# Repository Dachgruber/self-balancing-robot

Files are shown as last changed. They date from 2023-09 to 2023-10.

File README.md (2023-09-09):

# self-balancing-robot
Arduino code and building materials needed for the self-balancing-robot project for ElektronikFuerLA SoSe23 at CAU Kiel

## Hardware
The currently used hardware (MK1):
  -Arduino Nano (ATMega68p)
  -GY-521 Internal Measuring Unit
  -2x A4988 Stepper Motor Driver Boards
  -2x NEMA-17 0.48Nm Stepper Motors with D-Shaft
  -2200 mAh 40C 11.1V LiPo
  - 2 push buttons and 1 switch
  condensators, LEDs, wires...

Frame is build out of 10mm MDF-Plywood and 3mm craft wood sandwich plating
## Software

The code provided includes some testing programmes used at the R&D stage of development.

The finished piece of software will include:
  - a sensoring unit for measuring the current position
  - a calibration programm for calibrating said sensoring unit
  - a PID controller for controlling the two stepper motors
  - some form of remote control feature
and some more quality of life features

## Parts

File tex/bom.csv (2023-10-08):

Label | Part Type | mn | mpn | part number
C1 | Electrolytic Capacitor
LED1 | Red (633nm) LED
LED2 | Green (555nm) LED
M1 | Stepper Motor - Bipolar
M2 | Stepper Motor - Bipolar
Part1 | Arduino Nano (Rev3.0)
Part2 | InvenSense MPU6050
Pololu A2 | Pololu A4988
Pololu A3 | Pololu A4988
R1 | 220Ω Resistor
R2 | 330Ω Resistor
R3 | 10kΩ Resistor
R4 | 10kΩ Resistor
R5 | Rotary Potentiometer (Small)
S1 | Round Pushbutton
S2 | Taiway 100-SP-X-T1 SPDT Miniature Toggle Switch |  |  | 100-SP-X-T1-0-0-B1-M1
S3 | Round Pushbutton
U1 | LIPO-2000mAh
Amount | Part Type | mn | mpn | part number
2 | 10kΩ Resistor
1 | 220Ω Resistor
1 | 330Ω Resistor
1 | Arduino Nano (Rev3.0)
1 | Electrolytic Capacitor
1 | Green (555nm) LED
1 | InvenSense MPU6050
1 | LIPO-2000mAh
2 | Pololu A4988
1 | Red (633nm) LED
1 | Rotary Potentiometer (Small)
2 | Round Pushbutton
2 | Stepper Motor - Bipolar
1 | Taiway 100-SP-X-T1 SPDT Miniature Toggle Switch |  |  | 100-SP-X-T1-0-0-B1-M1

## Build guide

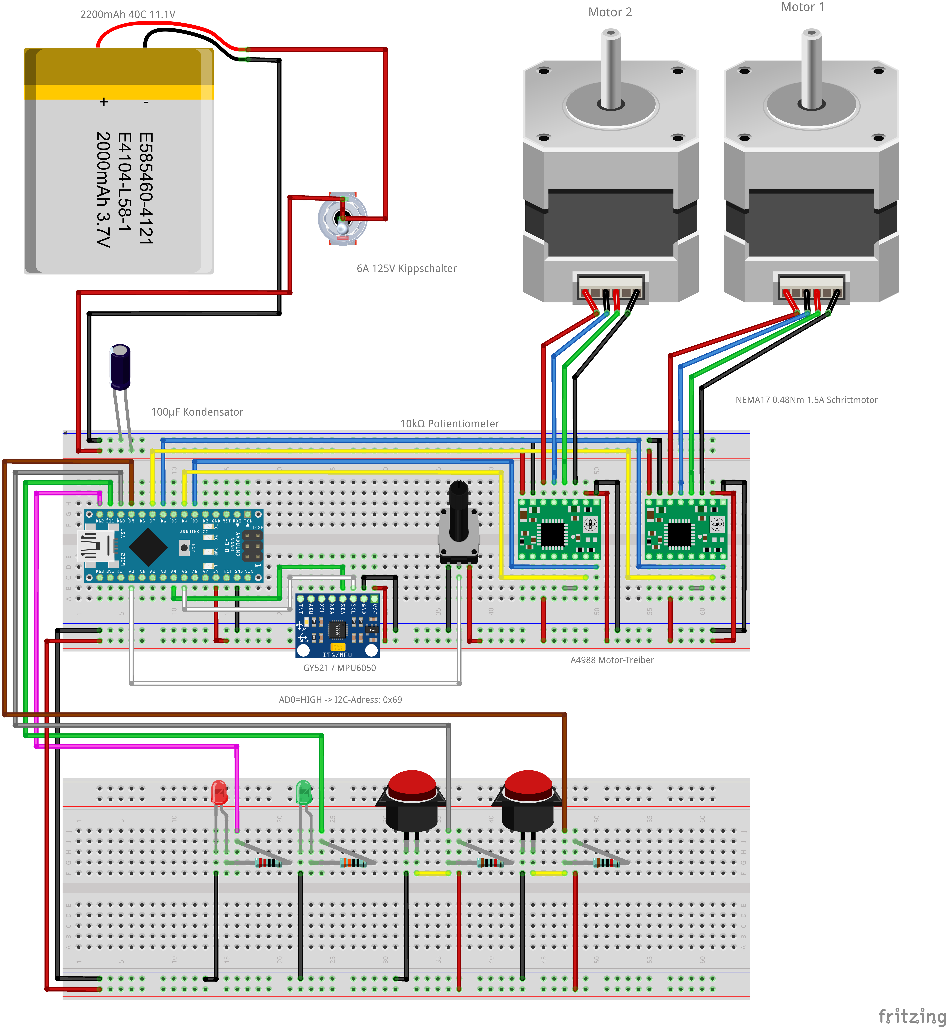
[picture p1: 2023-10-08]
tex/img/aufbau_breadboard.png

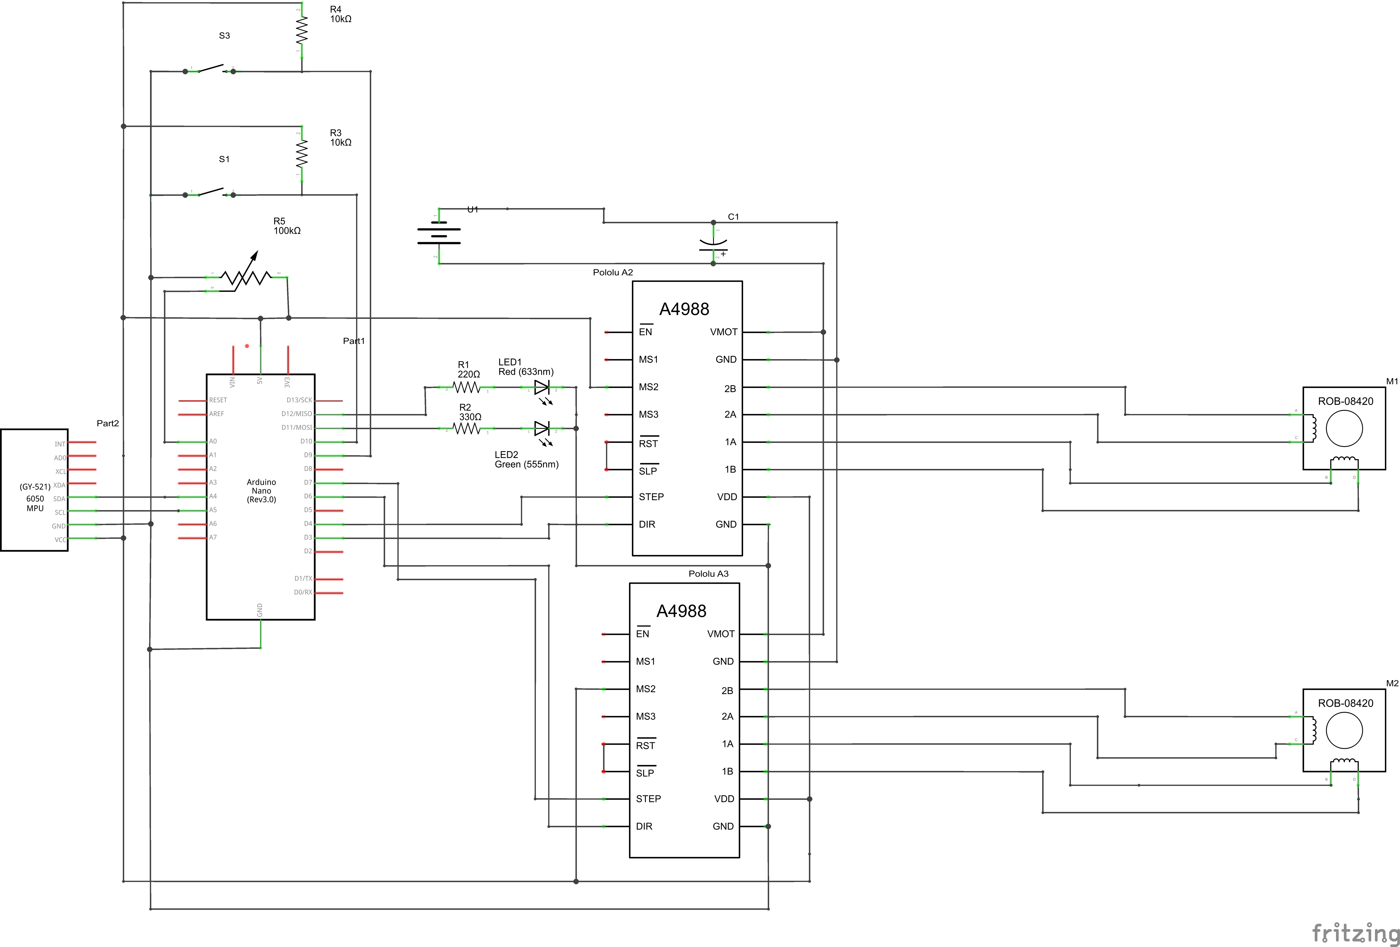
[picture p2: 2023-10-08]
tex/img/aufbau_scematic.png

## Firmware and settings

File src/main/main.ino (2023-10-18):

/*
* This is the main code used for the balancing robot. Flash this to the Arduino Nano Memory
* 
* This software will determine the current angle of the robot and will try to correct it to the desiredAngle constant usind the PID controller
*
* Used Wheels: d=70mm -> U = pi * d = 220mm
* Rotation = 200 Steps/rev * MicroStep -> 1000 Steps/rev
* 
* MaxSpeed = 1000 Steps/Second = 1 rev/s = 220mm/s
* 
* Höhe Schwerpunkt h = 240mm
* Schräglage theta = 20 degrees
*
* Zu korrigierende Länge x = h * sin (theta) = 82.08mm
*
* --> Bei einer Schräglage von 20 Grad ist Aropa theoretsch im Stande, die notwendige Länge bei MaxSpeed = 1000 in 0.4s zu überwinden
*
*/
//=============================================HEAD=======================================================
//used libraries
#include "math.h" 
#include <AccelStepper.h>
#include "KalmanMPU6050.h"
#include <PID_v1.h>

//math constants
#define earthConst 9.81

//DEBUG MODE enables serial output
const bool DEBUG = true;

//-----------------------------------------------Pins----------------------------------------------------

//two motor driver boards on two set of pins
#define dirPin1 3
#define stepPin1 4
#define dirPin2 6
#define stepPin2 7

#define potiPin A0

//no pins for the MPU as it gets detected on the I2C Bus
//#########################################CONFIG/TUNING ZONE###############################################

// params for the steppies
const int microStepConfiguration = 4; //1 for fullstep, 2 for halfstep, 4 for quarterstep...
const float maxSpeedLimit = 360 * microStepConfiguration * 2;
const float maxAccelLimit = 8000;

// three dabloons for the three parameters of the P I D
float KP = 16;   //(P)roportional Tuning Parameter
float KI = 0;   //(I)ntegral Tuning Parameter 
float KD = 0.0; //(D)erivative Tuning Parameter

//this is the angle in degrees the robot should be standing at, measured perpendicular to ground.
//the bias is used to account for a slanted positioning of the MPU (determine this using the mpu test) 
float angleBias = -2.5;
float targetAngle = 0 + angleBias;


//##########################################################################################################


//---------------------------------------------stepper setup----------------------------------------------

//stepper Objects used in the code
AccelStepper rightStep(AccelStepper::DRIVER,stepPin2,dirPin2);
AccelStepper leftStep(AccelStepper::DRIVER,stepPin1,dirPin1);  

//working var that specifies the current motorPower
volatile int motorPower;

//---------------------------------------------sensor setup----------------------------------------------
//working vars for the accelerometer and gyro
volatile float theta;


//-----------------------------------------------PID setup----------------------------------------------
//find KI,KP and KP in the Config Zone (tm)

//error working vars for the PID algorithm
volatile float error, prevError = 0, errorSum = 0;

//some time working vars //TODO: currently unused?
unsigned long currTime, prevTime = 0, loopTime;
float sampleTime = 0.005;

//find the desired angle in the Config Zone (tm)

//values used for the complimentary filter
float time = 0.9;
float alpha = time / (time + sampleTime);
float currentAngle, previousAngle;


//PID vars
//Define Variables we'll be connecting to
double setpoint, input, output;

//Specify the links and initial tuning parameters
PID myPID(&input, &output, &setpoint,2,5,1, DIRECT);
//============================================= TWIDDLE =======================================================

#include "Twiddle.h"
//const  bool AutoTuning = true;  // sets Twiddle on
const bool AutoTuning = false;

Twiddle Tuning(3,     KP,    KI,    KD, 0, 0, 0, 0, 0, 
                    0.005, 0.001, 0.001, 0,0,0,0,0);
//============================================= BODY =======================================================

void setup() {

  //because we do not want to explode the steppies
  rightStep.setMaxSpeed((float)maxSpeedLimit);
  leftStep.setMaxSpeed((float)maxSpeedLimit);

  //init the current Position
  leftStep.setCurrentPosition(0);
  rightStep.setCurrentPosition(0);

  //and determine the acceleration constant
  leftStep.setAcceleration(maxAccelLimit);
  rightStep.setAcceleration(maxAccelLimit);

  Serial.begin(9600);
  //Wire object is included the IMU lib atm
  //Wire.begin();
  //delay(100); //delay to rule out some issues with Wire being slow

  //mpu setup
  IMU::init();
  IMU::read();

  //enable the ISR timer routine
  initISR();

  //PID lib inits
  input = 0;
  setpoint = targetAngle;  
  myPID.SetOutputLimits(-360, 360);
  myPID.SetControllerDirection(1);

  Serial.println("SETUP COMPLETED");
  delay(1000);

}


/*
* util function that works like map, but for floats instead of integers
*/
float floatMap(float x, float in_min, float in_max, float out_min, float out_max) {
  return (x - in_min) * (out_max - out_min) / (in_max - in_min) + out_min;
}


/*
* Reads the onboard potentiometer and maps the analog value
* to a float between minV and maxV
*
*/
float readPoti(int minV, int maxV) {
  int analogValue = analogRead(potiPin);
  float finValue = floatMap(analogValue, 0, 1023, minV, maxV);

  return finValue;
}


void loop() {

  //read the tuning value of the poti
  //KP = readPoti(0,50);
  
  KD = readPoti(0,5);

  if  (AutoTuning)  PIDAutoTuning();  

  if (DEBUG) {
    Serial.print("KP:"); Serial.print(KP); Serial.print(" "); 
    Serial.print("KI:"); Serial.print(KI); Serial.print(" ");
    Serial.print("KD:"); Serial.print(KD); Serial.print(" ");
  }

  //Reads the data from the MPU...
  IMU::read();

  //...and processes it with the Kalman Filter
  theta = IMU::getRoll();

  //compute the needed motorpower using the PID
  //this sets the global motorPower to a new value
  //computePID();

  myPID.SetMode(AUTOMATIC);
  myPID.SetTunings(KP,KI,KD);
  input = theta;
  myPID.Compute();
  motorPower = output;

    if (DEBUG) {
    Serial.print("Current_Angle:");
    Serial.print(theta);
    Serial.print(",");
    Serial.print("Motor_Power:");
    Serial.println(motorPower);
  }


  //and set the Motors using the motorPower variable
  setMotors(motorPower, motorPower);

}

/* some register magic taken and from instructables and modified to my needs
*  LINK: https://www.instructables.com/Arduino-Self-Balancing-Robot-1/
* 
*  This enables the internal Timer1 to interrupt the loop routine every 5ms
*  The time depends on the setting of the prescaler TCCR1B and the Counting 
*  register OCR1A
*  
*  Example Calculations (for 500ms): 
*  System clock 16 Mhz and Prescalar 256;
*  Timer 1 speed = 16Mhz/256 = 62.5 Khz    
*  Pulse time = 1/62.5 Khz =  16us  
*  Count up to = 500ms / 16us = 31250 (so this is the value the OCR register should have)  
*/
void initISR(){
  cli(); // disable global interrupts
  TCCR1A = 0; //set entire TCCR1A register to 0, resetting the timer value
  TCCR1B = 0; //same for TCCR1B
  //set compare match register to set sample time 5ms
  OCR1A = 100;
  //prescale: will divide the clock signal with 8, slightly slowing down our timer
  //TCCR1B |= (1 << CS11);
  TCCR1B |= B00000010;
  // enable timer compare interrupt
  TIMSK1 |= (1 << OCIE1A);
  sei(); //enable global interrupts

} 

/*
* The Interrupt Service Routine (ISR) looks like a function
* that gets called in the specified timing intervall
*
* Our ISR will be called every 5ms to execute our run()
*/
ISR(TIMER1_COMPA_vect) {
  TCNT1  = 0; //reset the timer 
  // calling run() instead of runSpeed() tells the stepper to
  // accelerate to maxSpeed instead of using constant Speed
  leftStep.run();
  rightStep.run();

}
/*
* computes the new motorPower value using a PID-algorithm 
* We currently do not depend on the ISR for this call but instead call the PID function 
* from the main loop func ourselfs. This means that is isnt quite clear how much time
* lays inbetween calls, which will cause troubles later (foreshadowing)
*
* -> motorPower is a global variable because it needs to be when using the ISR
*
* This algorithm will do the following steps:
*
*     1. take the measured (and filtered!) angle from the mpu
*     2. compute the PID error that specifies, how "bad" the current situation is
*     3. compute the Proportional, Integral and Derivative terms of the PID with the magic KP,KI and KD numbers and errors
*     4. add the terms (and constrain the result!) the to calculate the needed motorPower (no return needed as motorPower is global)
*/
void computePID() {  

  /*1. take the angle */
  currentAngle = theta;

  if (DEBUG) {
    Serial.print("Current_Angle:");
    Serial.print(currentAngle);
    Serial.print(",");
  }

  /*2. error calculation*/
  //calculation of error values for the PID
  error = currentAngle - targetAngle;
  errorSum = errorSum + error;
  errorSum = constrain(errorSum, -300, 300); //damit uns die Geschichte nicht um die Ohren fliegt

  /*3. error calculation*/
  //calculate output from P, I and D values
  float pValue,iValue,dValue;
  pValue = KP * (error);
  iValue = KI * (errorSum)*sampleTime;
  dValue = KD * (currentAngle-previousAngle)/sampleTime;

  /*4. final steps*/
  float output = pValue + iValue - dValue;
  //a circle has 360 degrees, so constrain to one circle in each direction
  motorPower = constrain(output, -360, 360); 
  previousAngle = currentAngle; //save for next time

}

/*
* Function for controlling the left and right motor using a distance in degrees (°)
* positive values mean forward, negative mean backward rotation
*
*/
void setMotors(float leftDistance, float rightDistance){

  leftStep.move(leftDistance);
  rightStep.move(-rightDistance);

}

void  PIDAutoTuning()  //Twiddle Auto Tuning
// --------------------------------------------------------------
{
  static int skipT = 0;
  skipT++;
  if (skipT > 10) {
    skipT = 11;

    // average = Tuning.next( Robot.PositionAB, PidParams.Kp , PidParams.Ki , PidParams.Kd  ,  PidParams.Ka , PidParamsPos.Kp , PidParamsPos.Ki , PidParamsPos.Kd , PidParamsPos.Ka  );

    average = Tuning.next( (currentAngle), KP  , KI , KD , 0, 0 , 0  , 0 ,  0  );

  }
}



/*
* @deprecated
* This adds the gyro and accel angle using a comp filter
*
*/
//float addAngle(float gyro, float accel) {

  //calc the current angle depending on the measured data

  //accAngle = atan2(accY, accZ)*RAD_TO_DEG;
  //gyroRate = map(gyroX, -32768, 32767, -250, 250); //mapping gyroX to int range 2^16 = 65 534
  //gyroAngle = (float)gyroRate*sampleTime;
  //gyroAngle = gyroX;

  /*2. combination of angles*/
  //combining acc and gyro values using a complementary filter
  //filter acts as a high pass on the gyro and a lowpass on the accel to filter out drift from gyro and noise from accel
  //float addedAngle = 0.0;
  //addedAngle = alpha * (previousAngle + gyroAngle + sampleTime) + (1-alpha) * (accAngle);

  //return addedAngle;
//}

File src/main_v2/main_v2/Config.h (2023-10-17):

/* Self balancing Robot via Stepper Motor with microstepping and Digital Motion Processing
    written by : Rolf Kurth in 2019
    rolf.kurth@cron-consulting.de
    modified by : Cornelius Brütt in 2023

*/
#ifndef   Config_h
#define  Config_h
#include "Arduino.h"
//#include "Filter.h"


/*   PIN Belegung
  for a complete setup overview, please refere to the fritzing sketch in the hrdw directory
  D3  Dir   Motor1
  D4  Step  Motor1
  
  D6  Dir   Motor2
  D7  Step  Motor2

  D9  ButtonInput Button1
  D10 ButtonInput Button2
  D11 LED1
  D12 LED2

  A0  Poti Input

  A4  SDA MPU
  A5  SCL MPU

*/

//we do not use any interrupts as we implement a polling strategy

#define LED_PIN = 11;


const int  PinDirMotorA  = 3;
const int  PinDirMotorB  = 6;
const int  PinStepMotorA  = 4;
const int  PinStepMotorB   = 7;

const int  TuningPin      = A0; //Potentiometer


struct MpuYawPitchRoll   {
  float yaw, pitch, roll;
};


#endif

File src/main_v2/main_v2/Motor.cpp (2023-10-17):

/* Self balancing Robot via Stepper Motor with microstepping and Digital   Motion Processing
    written by : Rolf Kurth in 2019
    rolf.kurth@cron-consulting.de
    modified by : Cornelius Brütt in 2023

   Stepper Motor: Bipolar, 200 Steps/Rev, 4023mm, 12V, 1.5 A/Phase
  https://www.pololu.com/product/1200/faqs
   This NEMA 17-size hybrid stepping motor can be used as a unipolar or bipolar stepper   motor
  and has a 1.8 step angle (200 steps/revolution). Each phase draws 0.3   A at 12 V,
  allowing for a holding torque of 4.28 kg-cm (0.42Nm)

  Wheel diameter d= 70mm => Distance per Pulse Dpp = d * pi / 200 =  1,0996 mm
  Distance per Revolution =  pi * d = 219.911 mm
  Max 1000 Steps per Second = 5 Revolutions => 1099.55 mm Distance per Second

  Motion Control Modules  Stepper Motor Drivers  A4988 Stepper   Motor Driver Carriers
  https://www.pololu.com/product/1182

  The Motor Driver can be adjusted for different microstep resolutions. In the ARoPA MK-I, these will be fixed
  so no changing in software is possible.

  MS1 	MS2 	MS3 	Microstep Resolution
  Low 	Low 	Low 	Full step
  High 	Low 	Low 	Half step
  Low 	High 	Low 	Quarter step
  High 	High 	Low 	Eighth step
  High 	High 	High 	Sixteenth step
*/

#include   "Motor.h"
#include "Config.h"
/**********************************************************************/
//Motor::Motor(DuePWMmod*   ipwm, int iPinDir, int iPinStep,  char iMotorSide )
Motor::Motor(int iPinDir, int iPinStep,  int iMotorSide )
/**********************************************************************/
{
  _PinStep   = iPinStep;
  _PinDir    = iPinDir;
  _MotorSide = iMotorSide;

  pinMode(_PinDir,   OUTPUT);
  pinMode(_PinStep,   OUTPUT);

  ptr =   (int) this;
  //ptrpwm = ipwm;

  _Divisor = 8; //because we use 1/8 microstepping atm
}
/**********************************************************************/
Motor*   Motor::getInstance()
/**********************************************************************/
{
  pMotor = this;
  return pMotor;
}
/**********************************************************************/
void   Motor::init ( )
/**********************************************************************/
{

  Serial.print("Motor ");
  Serial.print(ptr , HEX);
  Serial.print(" Side   ");
  Serial.print(_MotorSide);
  Serial.print(" iPinStep ");
  Serial.print(_PinStep);
  Serial.println("   init...");
  lastTime = millis();

}
/**********************************************************************/
void   Motor::SleepMode( )
/**********************************************************************/
{
  MotorMode = false;
}
/**********************************************************************/
void   Motor::RunMode( )
/**********************************************************************/
{
  MotorMode = true;
}
/**********************************************************************/
void   Motor::toggleMode( )
/**********************************************************************/
{
  if ( MotorMode == false ) RunMode( );
  else  SleepMode();
}
/**********************************************************************/
float   Motor::Run(float Steps) {
/**********************************************************************/
  if (!MotorMode)   {
    RunMode( );

    if (_MotorSide == 1) {
      if (Steps   >= 0 ) {
        digitalWrite(_PinDir, LOW);
        DirForward = true ;
       }
      else {
        digitalWrite(_PinDir, HIGH);
        DirForward   = false ;
      }
    } else
    {
      if (Steps >= 0 ) {
        digitalWrite(_PinDir,   HIGH);
        DirForward = true ;
      }
      else {
        digitalWrite(_PinDir,   LOW);
        DirForward = false ;
      }
    }

    if (_Divisor   > 0) {
      Steps = Steps * _Divisor; // convert into Microsteps
    }

     if ((abs(Steps) < 2.0))  Steps = 2.0;
    return Steps;
  }
  else   SleepMode( );
}

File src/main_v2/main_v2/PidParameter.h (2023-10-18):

/* Self balancing Robot via Stepper Motor with microstepping and Digital  Motion Processing
    written by : Rolf Kurth in 2019
    rolf.kurth@cron-consulting.de
    modified by : Cornelius Brütt in 2023
*/
#ifndef  PidParameter_h
#define  PidParameter_h
#include "PidParameter.h"

//  PidParameter Motor
struct PidParameter {
  float          K = 5.0;
  float          Kp =  9.4282 ;
  float          Ki =  5.5223;
  float          Kd  = 0.145;
  float          Ka = 0.1220;
  float          Kx = 0.0; //
};
//  PidParameter Position
struct PidParameterPos {
  float          K = 1.0;
  float          Kp = 0.0;
  float          Ki = 0.0;
  float          Kd  = 0.08 ;
  float          Ka = 0.0 ;
  float          Kx = 0.0;
};
#endif

//Step=  1 Ind= 0 av= 1.5500 besterr 0.0300 P0 9.4282 P1 5.5223 P2 0.1445 P3 0.1220 P4 0.03  P5 0.00 P6 0.02 P7 0.0000
//Step= 1 Ind= 0 av= 5.1000 besterr 0.0267 P0 0.0315  P1 0.0015 P2 0.0000 P3 0.0000 P4 9.43 P5 5.52 P6 0.14 P7 0.1220 
//Step= 1 Ind=  1 av= 4.6900 besterr 0.0133 P0 0.0336 P1 0.0025 P2 0.0010 P3 0.0000 P4 9.43 P5 5.52  P6 0.14 P7 0.1220 

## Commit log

2023-08-17 added new stepper lib
2023-08-17 added alternative lib test, although it does not work
    [mpu_other_lib_test.ino]
2023-08-17 added PID and motor control functions
2023-09-09 updated schematic and finished commenting
    [Balancing_Robot_V02.fzz]
2023-09-10 added button panel
    [Balancing_Robot_V02.fzz]
2023-09-20 added serial prints and fixed pin defs
    [button_panel_test.ino]
2023-09-20 fixed pins again because I am stupid
    [button_panel_test.ino]
2023-09-20 button panel now functioning, added explanation text
2023-09-20 added testing programm for the MPU board
2023-09-20 mpu is now functioning, fixed ic2 bus address
    [mpu_test.ino]
2023-09-20 minor fix
    [Balancing_Robot_V02.fzz]
2023-09-21 added test for steppers
2023-10-03 changed pin layout of stepperPins
2023-10-03 changed direction of stepper output
2023-10-05 changed to steps instead of velocity
2023-10-05 added new test files for next stage
2023-10-05 included new poti for easy PID tuning
2023-10-07 removed BT module and edited microstepping
    [Balancing_Robot_V02.fzz, Balancing_Robot_V03_ohne_BT.fzz]
2023-10-07 edited breadboard layout to fit into Ausarbeitung
    [Balancing_Robot_V03_ohne_BT.fzz]
2023-10-07 inital upload
    [bom.csv]
2023-10-08 fixed some minor bugs
    [main_abgabe.ino]
2023-10-17 implemented second PID lib and moved the old one
2023-10-17 added motor files
2023-10-17 added PWM lib
2023-10-18 tried some different motor approach
